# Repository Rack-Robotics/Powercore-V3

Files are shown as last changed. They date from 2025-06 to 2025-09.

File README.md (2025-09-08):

# Powercore V3

A high-efficiency power supply unit designed for Electrical Discharge Machining (EDM) applications.

## Repository Structure

- `circuit-boards/` - KiCAD PCB designs for all modules
- `schematics/` - Schematic PDFs for electronics
- `KiCAD-library/` - Custom component library and 3D models
- `LTSpice/` - Simulation files
- `powercoreV3-firmware/` - Arduino firmware for the RP2040 controller

## Table of Contents

- [PSU HIGHLIGHTS](#psu-highlights)
- [FEATURES](#features)
- [APPLICATIONS](#applications)
- [GENERAL DESCRIPTION](#general-description)
- [SPECIFICATIONS](#specifications)
- [Recommended Operating Conditions](#recommended-operating-conditions)
- [DEVICE INTERFACES](#device-interfaces)
  - [Power Input Connector](#power-input-connector)
  - [Power Output Connector](#power-output-connector)
  - [Digital Interface Connector](#digital-interface-connector)
  - [USB-Micro Serial Interface](#usb-micro-serial-interface)
- [THEORY OF OPERATION](#theory-of-operation)
- [OPERATION MODES](#operation-modes)
  - [Startup Behavior](#startup-behavior)
  - [Idle Mode](#idle-mode)
  - [Iso-Frequency Mode](#iso-frequency-mode)
  - [Edge-Detection Mode](#edge-detection-mode)
- [APPLICATION EXAMPLE: MINIMUM IMPLEMENTATION](#application-example-minimum-implementation)
- [EMC & EMI](#emc--emi)
- [Images of PCBA](#images-of-pcba)
- [Typical PSU Waveforms](#typical-psu-waveforms)
- [LICENSE](#license)
- [⚠️ HIGH VOLTAGE SAFETY WARNING ⚠️](#️-high-voltage-safety-warning-️)

## PSU HIGHLIGHTS

1. Optimized for wire EDM applications
2. Maximum input power: 300W with high efficiency topology
3. Adjustable output parameters:
   - Machining Duty Cycle: 1% to 10%
   - Spark Initiation Voltage: 64V to 100V
   - Machining Frequency: 5kHz to 10kHz
4. USB serial interface for configuration and telemetry
5. PWM feedback output for external feedrate control
6. Edge detection capability for workpiece probing

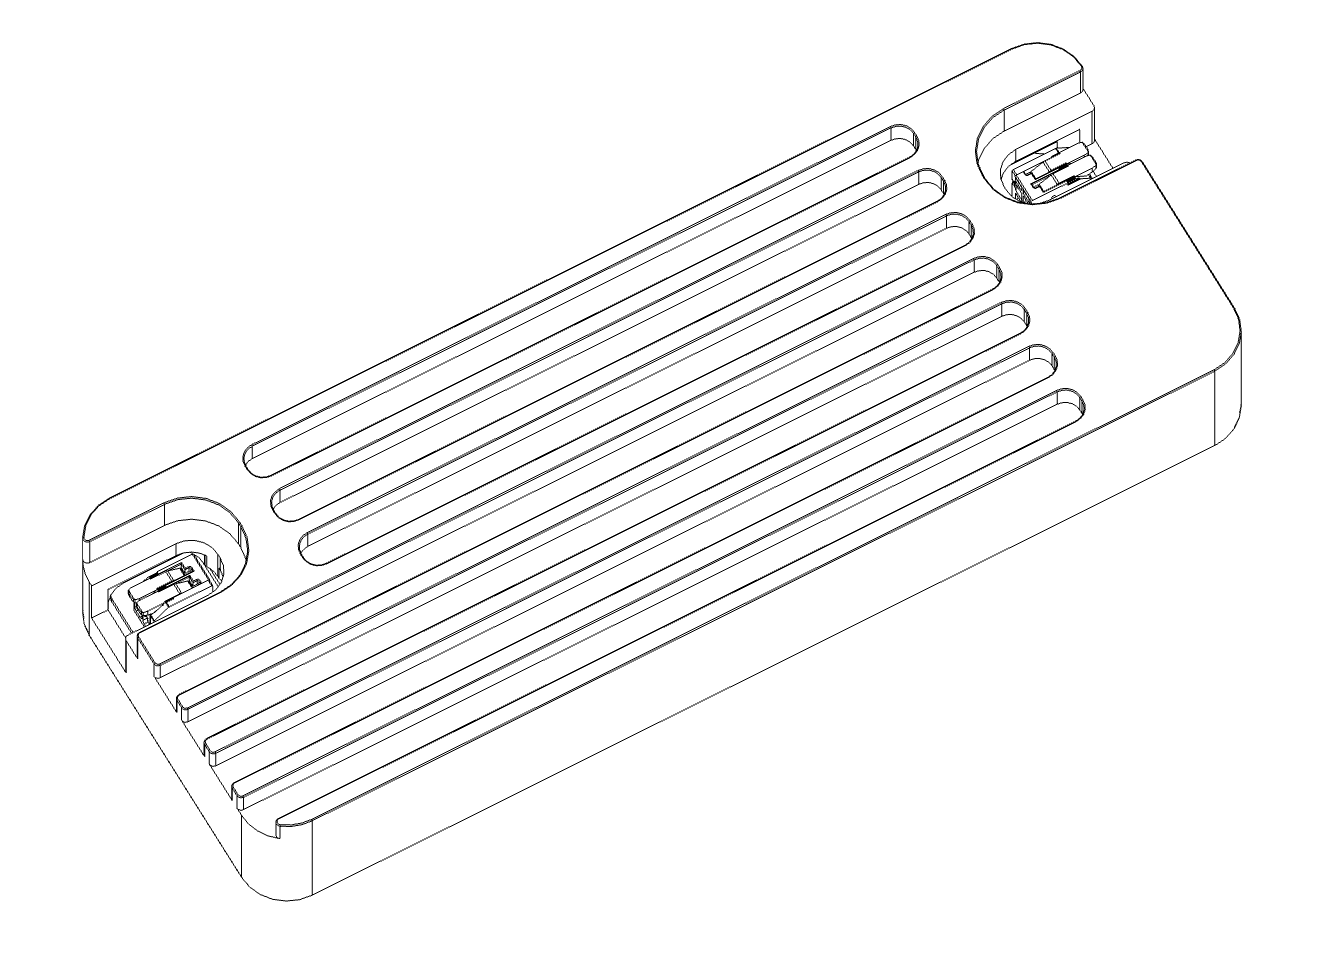
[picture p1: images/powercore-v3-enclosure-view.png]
Powercore V3 Enclosure View


## FEATURES

- **Dual-Converter Topology** with resonant converter and boost converter for high-efficiency EDM machining
- Input power optimized for desktop/micro-scale wire EDM (300W maximum, 48V input)
- Output parameters configurable via USB-micro serial interface
- Integrated protection features: pulse-skipping, overcurrent protection, and inrush protection
- Open-source electronics, firmware, and CAD files

## APPLICATIONS

- Wire EDM
- Plunge EDM
- Desktop-scale EDM machines
- Portable and battery-powered EDM machines
- Scientific research and development

## GENERAL DESCRIPTION

The Powercore V3 provides precision control of machining parameters including duty cycle, spark initiation voltage, and machining frequency. The system is optimized for desktop-scale wire EDM applications. The open-source design enables customization for research, development, and specialized EDM implementations.

## SPECIFICATIONS

| SPECIFICATION | Min | Max Value | UNIT |
| --- | --- | --- | --- |
| Average Input Power | 10 | 300 | W |
| Input Voltage | 47.8 | 48.2 | V |
| Input Current | 0.625 | 6.25 | A |
| Machining Duty Cycle | 1 | 10 | % |
| Spark Initiation Voltage | 64 | 100 | V |
| Machining Frequency | 5,000 | 10,000 | Hz |
| Machining Current (1) | 40 | 70 | A |
| PWM Feedback Duty Cycle | 0 | 100 | % |
| PWM Feedback Voltage | 0 | 3.3 | V |
| PWM Feedback Frequency  | — | 1,000 | Hz |
| PWM Feedback Output Impedance | 1,010 | 9,990 | Ω |
| Enable Input Voltage | 3.0 | 3.5 | V |
| Enable Input Impedance | 1,010 | 9,990 | Ω |

(1) Machining current depends on output cable impedance and discharge characteristics. Not regulated by constant-current control. Lower-impedance output cables provide higher machining current.

## Recommended Operating Conditions

| Parameter | Value |
| --- | --- |
| Ambient Temperature | 0°C to 30°C |
| Ingress Protection Rating | IP20 (Indoor use) |
| Relative Humidity | 20% to 80% (non-condensing) |
| Input Cable Gauge | 16 AWG minimum |
| Output Cable Gauge | 16 AWG stranded, 300V rated |
| Output Cable Length | <1 meter, twisted pair |
| Cooling | Forced air cooling recommended |

## DEVICE INTERFACES

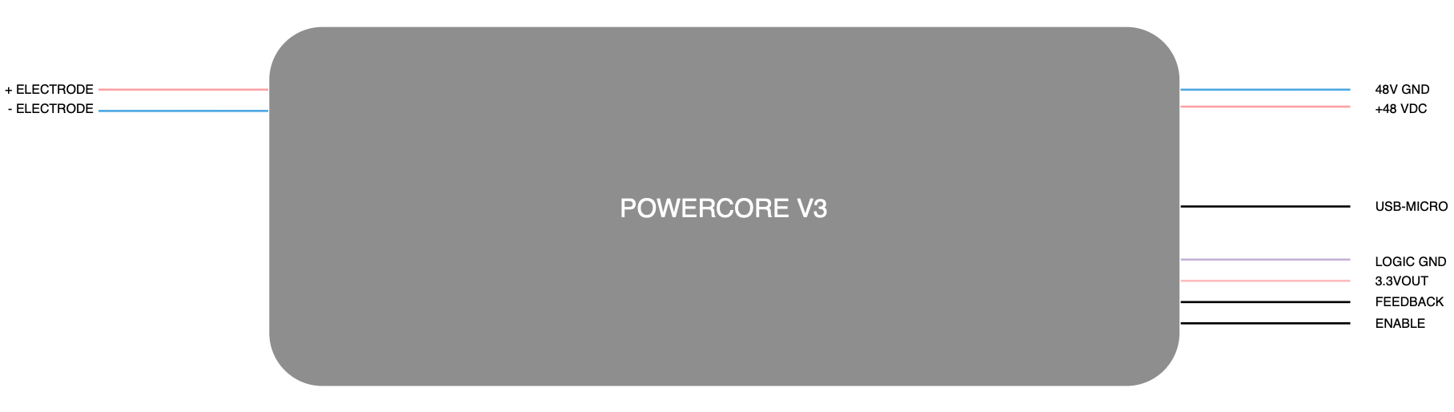
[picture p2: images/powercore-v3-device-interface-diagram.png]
Powercore V3 Device Interface Diagram


### POWER INPUT CONNECTOR

Input power connects via 2-position lever-action Wago connector accepting 16 AWG conductors. 48VDC input must be connected before applying 5V via USB-micro. If USB power is applied before 48VDC input, the microcontroller enters fault mode.

### POWER OUTPUT CONNECTOR 

Output connects via 2-position lever-action Wago connector accepting 16 AWG stranded conductors. Output cable must be twisted pair, <1 meter length, and either shielded/grounded or contained within a shielded/grounded enclosure.

### DIGITAL INTERFACE CONNECTOR 

4-position JST-XH header provides communication with external controllers. Exposes 3.3V and GND from RP2040 microcontroller with current-limiting resistors.

- **Enable Input**: Output is enabled when this input is connected to 3.3V or external 3.3V supply with common ground. 10kΩ pull-down resistor to GND.
- **Feedback Output**: Reports EDM power consumption via active-low PWM signal. 100% duty cycle indicates no power consumption from machining; 0% indicates short circuit. Maintain 10-90% duty cycle during machining by adjusting feedrate. 10kΩ pull-down resistor to GND. External low-pass filter can convert to analog feedback.

### USB-MICRO SERIAL INTERFACE

Exposes USB-micro connector of RP2040 Pico module for parameter configuration and telemetry. Default baud rate: 115,200.

**Warning**: Device requires both 48VDC input power AND 5V USB power. 48VDC must be connected first, or device enters fault mode.

| SERIAL COMMAND | DESCRIPTION |
| --- | --- |
| SEND_TELEMETRY | Request device status and parameters |
| SET_ALL_PARAMETERS | Configure machining parameters: discharges, duty cycle, frequency, initiation voltage<br>Format: 'SET_ALL_PARAMETERS [discharges] [duty_cycle] [frequency] [voltage]'<br>Example: 'SET_ALL_PARAMETERS 0 0.10 5000 100' |
| EDM_ISOFREQUENCY_MODE | Enter EDM iso-frequency mode |
| EDGE_DETECTION_MODE | Enter edge detection mode |
| RESET_DEVICE | Reset device |

Invalid commands return list of valid commands.

## THEORY OF OPERATION

The Powercore V3 generates controlled electrical discharges for EDM machining. The system cycles through spark initiation, current delivery, and discharge termination at high frequency (5-20kHz).

**Spark Initiation Voltage**: Determines spark formation conditions. Higher voltages create longer, more intense discharges suitable for harder materials.

**Machining Duty Cycle**: Controls discharge duration. Longer duty cycles increase material removal rate but may increase surface roughness.

**Machining Frequency**: Sets discharge repetition rate. Lower frequencies can increase material removal rate but may reduce surface finish quality.

**Machining Current**: Ranges from 40A to 70A, determined by fixed 48VDC output during current phase and combined impedance of output cables and discharge gap. Current is not user-adjustable.

## OPERATION MODES

### STARTUP BEHAVIOR 

On power-up, output is disabled (high-impedance state). Power management module initializes and pi-filter capacitors charge to 48V with inrush protection. Brief audible noise (~1 second) is normal during startup. Output current sensor calibrates and serial communication establishes.

**BOOST CONVERTER SELF-TEST**: System tests boost converter module and I2C digital potentiometer. If I2C communication fails, device reports 'ERROR: DPOT is not at expected position'. 

During startup, digital potentiometer cycles through settings 0-110, generating boost converter output voltage lookup table (50V-160V). If voltage range is insufficient, device enters fault mode and reports 'ERROR: DPOT voltage range is less than expected'.

Normal startup sequence via serial:
```
Setting DPOT to minimum position...
Waiting for voltage to stabilize...
Reading voltages for DPOT lookup table...
Boost Converter Digital Potentiometer Voltage Table:
0: 51
1: 52
...
109: 161
110: 166
```

Successful startup indicated by solid green LED and "Setup complete" message. Device enters IDLE mode.

### IDLE MODE

Output remains in high-impedance state until enable input is asserted (3.3V). No discharges occur in idle mode.

### ISO-FREQUENCY MODE

Fixed-frequency discharge mode. Default mode or activated via 'EDM_ISOFREQUENCY_MODE' command. Enable input must be asserted (3.3V) to begin operation.

**ISO-FREQUENCY MODE PARAMETERS**

| PARAMETER | Min | Default | Max | Unit |
| --- | --- | --- | --- | --- |
| Machining Duty Cycle | 1 | 10 | 10 | % |
| Machining Frequency | 5,000 | 1,000 | 10,000 | Hz |
| Spark Initiation Voltage | 64 | 80 | 100 | V |

### EDGE-DETECTION MODE

Probe mode for detecting electrode-workpiece contact via PWM feedback. Intended for setup and calibration only, not for machining. Activated via 'EDGE_DETECTION_MODE' command with enable input asserted.

## APPLICATION EXAMPLE: MINIMUM IMPLEMENTATION

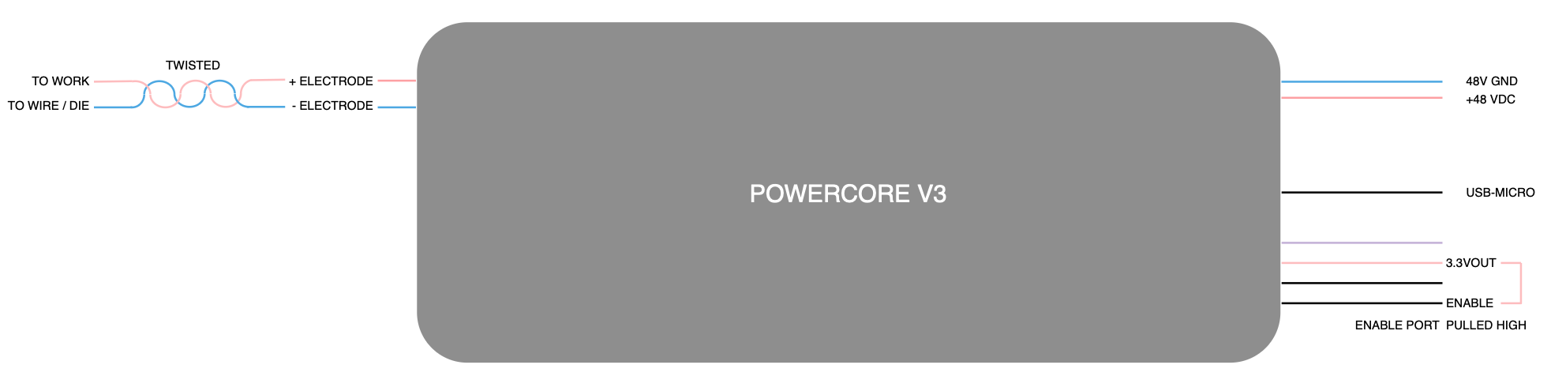
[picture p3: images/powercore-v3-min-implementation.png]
Powercore V3 Minimum Implementation


Minimum system configuration:

| Connection | Requirements |
| --- | --- |
| Power Input | 48V, 300W supply via 16 AWG stranded wire |
| USB-Micro | 5V supply or PC connection. **Note**: 48V must be connected first |
| Enable Input | Connect to 3.3V after power supplies are connected |
| Power Output | Positive (+) to workpiece, negative (-) to electrode (wire/tool) |

## EMC & EMI

The Powercore V3 power supply unit is housed in a precision-machined, billet-aluminum enclosure, fully grounded to minimize electromagnetic interference. When no output cables are connected, radiated emissions are negligible. However, when output cables are attached, radiated emissions vary based on cable characteristics, including length, twist, and wire gauge.

**Requirements**: Output cables must be shielded, grounded, and twisted. Poor cable design may increase emissions and interfere with sensitive equipment.

**Installation**: Complete machining setup should be enclosed, shielded, and grounded. EMC compliance is installer's responsibility.

## Images of PCBA

### PCBA View 1
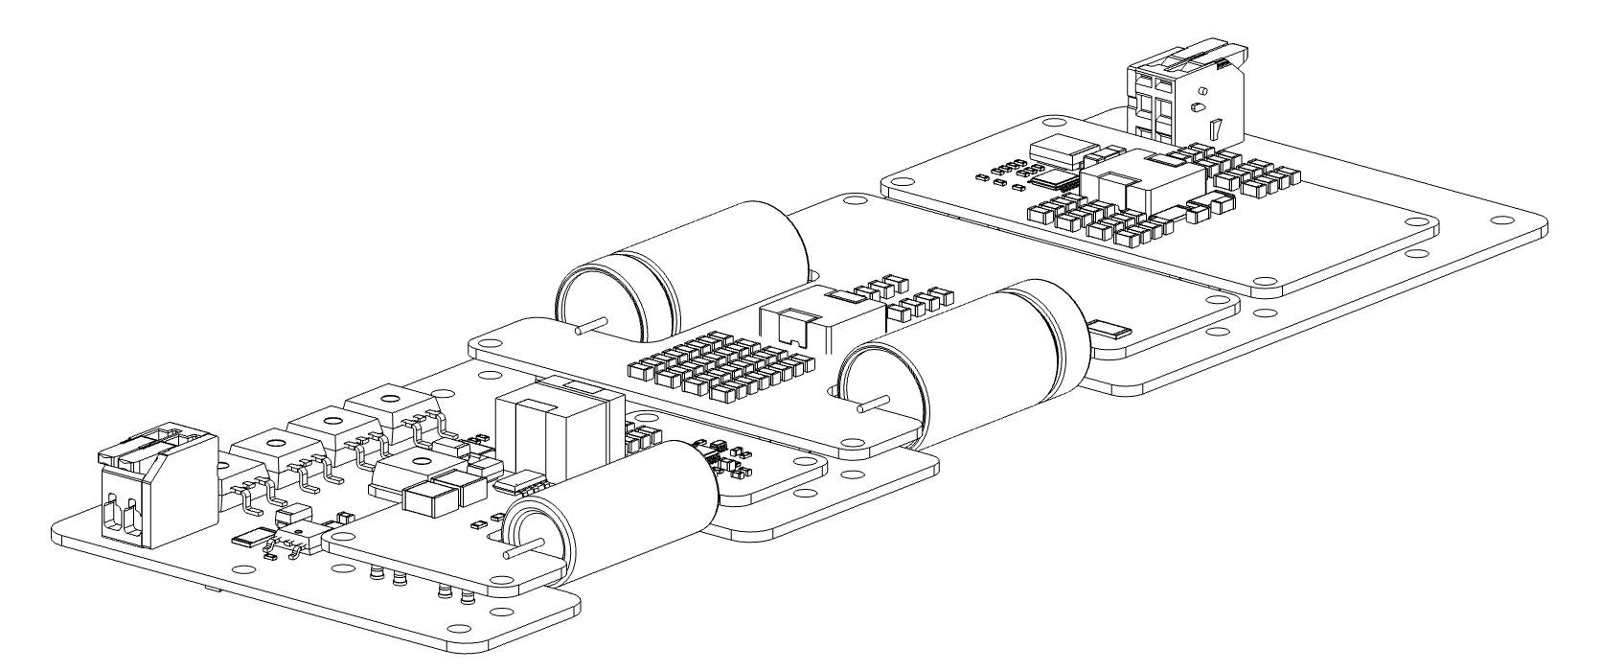
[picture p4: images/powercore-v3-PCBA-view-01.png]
Powercore V3 PCBA View 1


### PCBA View 2
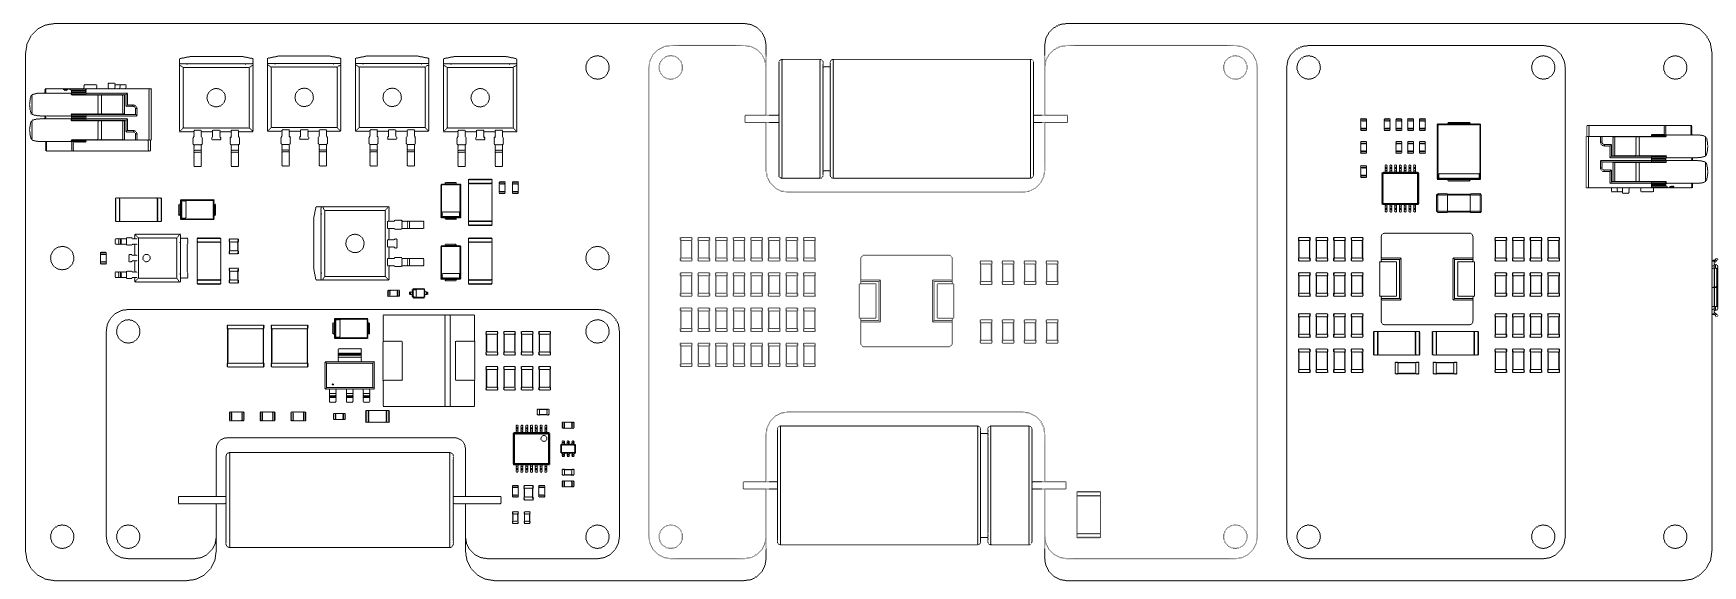
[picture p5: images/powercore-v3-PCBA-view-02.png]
Powercore V3 PCBA View 2


### PCBA View 3
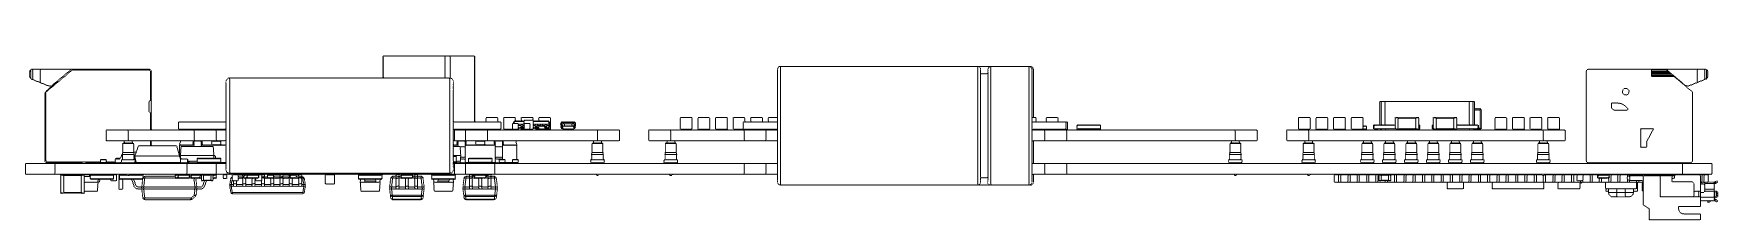
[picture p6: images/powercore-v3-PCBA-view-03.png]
Powercore V3 PCBA View 3


### PCBA View 4
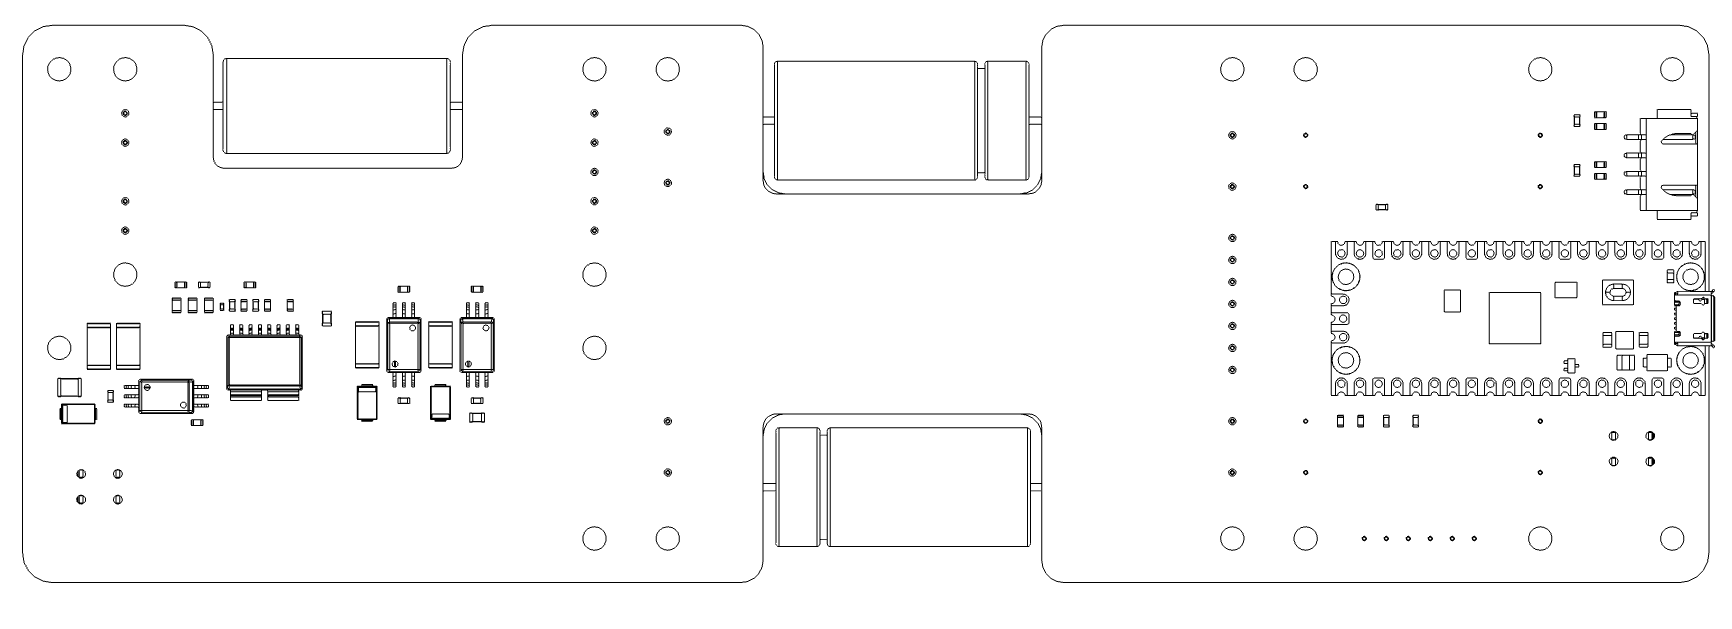
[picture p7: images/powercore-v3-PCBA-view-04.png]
Powercore V3 PCBA View 4


## Typical PSU Waveforms

### Output Stage Switch Control
Normal behavior of output stage switches during EDM iso-frequency mode. The enable (yellow trace) and high-current phase (red trace) switches are both active at the same time, permitting current flow from the positive electrode to the negative electrode. The high-voltage switch is active several microseconds before each switching event, for the purpose of charging the output capacitor to the spark initiation voltage (blue trace).

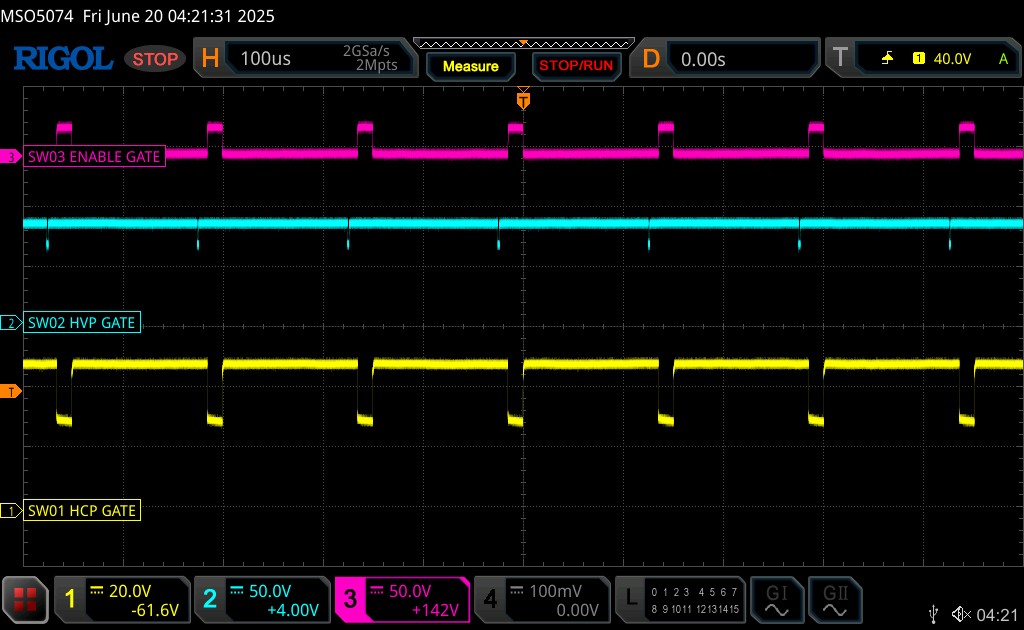
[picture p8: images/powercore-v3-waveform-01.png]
Powercore V3 Waveform 1


### Gap Voltage with Electrodes Separated
Normal behavior of output stages during EDM iso-frequency mode, with the electrodes separated by several millimeters under distilled water. The positive (+) electrode (red trace) shows the change in gap voltage when the output capacitor is charged and then slowly discharged through the water.

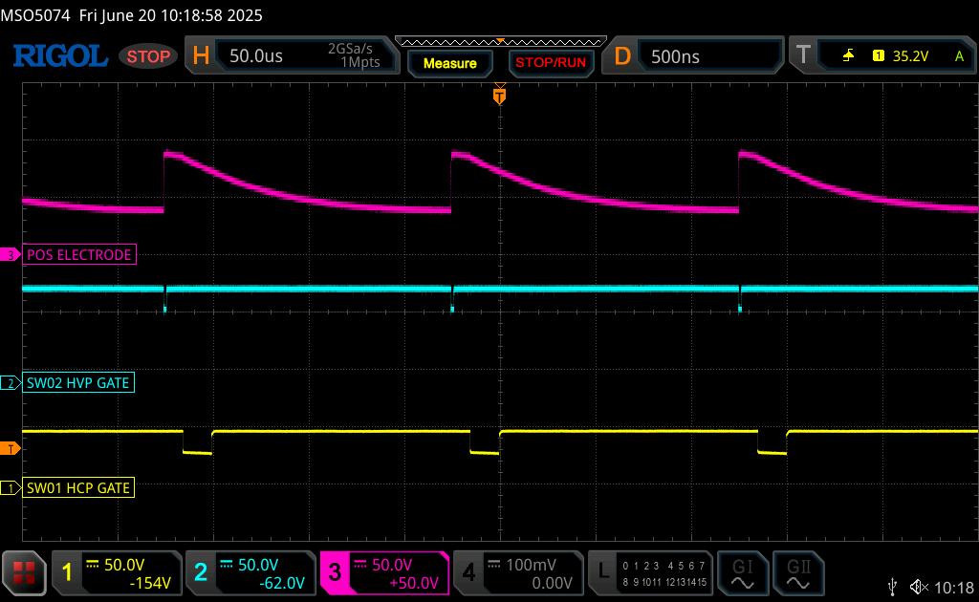
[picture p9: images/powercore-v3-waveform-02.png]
Powercore V3 Waveform 2


### EDM Discharge Behavior
Normal behavior of output stages during EDM iso-frequency mode, during electrical discharge machining. The positive (+) electrode voltage changes rapidly during an EDM discharge; transitioning from the spark initiation voltage (here 80V) to the gap machining voltage (~40V) in several hundred nanoseconds.

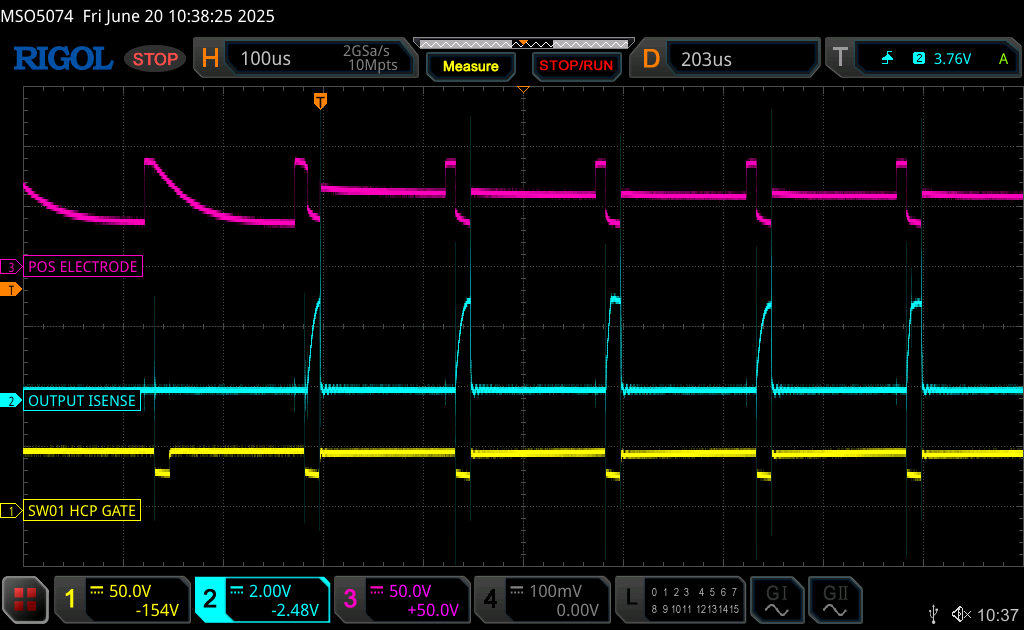
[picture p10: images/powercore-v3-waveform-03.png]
Powercore V3 Waveform 3


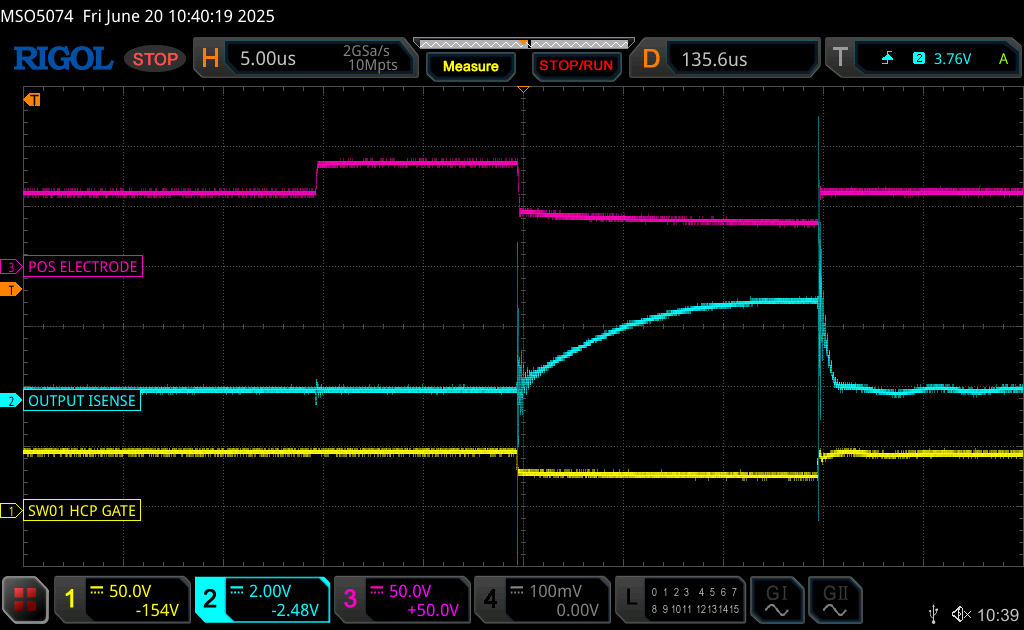
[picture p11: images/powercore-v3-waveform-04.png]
Powercore V3 Waveform 4


### Boost Converter Operation
Normal behavior of the boost converter module. The MOSFET gate (blue trace) presents with short pulses, which are used to maintain a stable output voltage. The output voltage will be set by the I2C digital potentiometer to between 64 and 150 V.

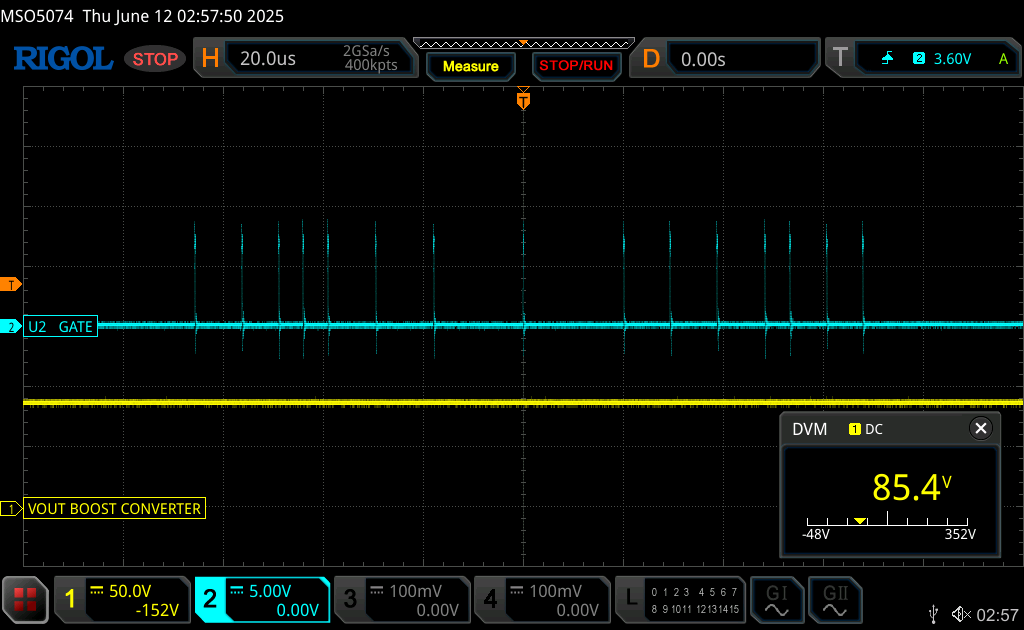
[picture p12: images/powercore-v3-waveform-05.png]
Powercore V3 Waveform 5


Startup behavior of device. Two seconds are required for inrush protection and serial communication initiation. Subsequently, the boost converter and output voltage sensor collaborate to create the lookup table for the I2C digital potentiometer. Once the lookup table is constructed, the boost converter is set to its default 80V setting.

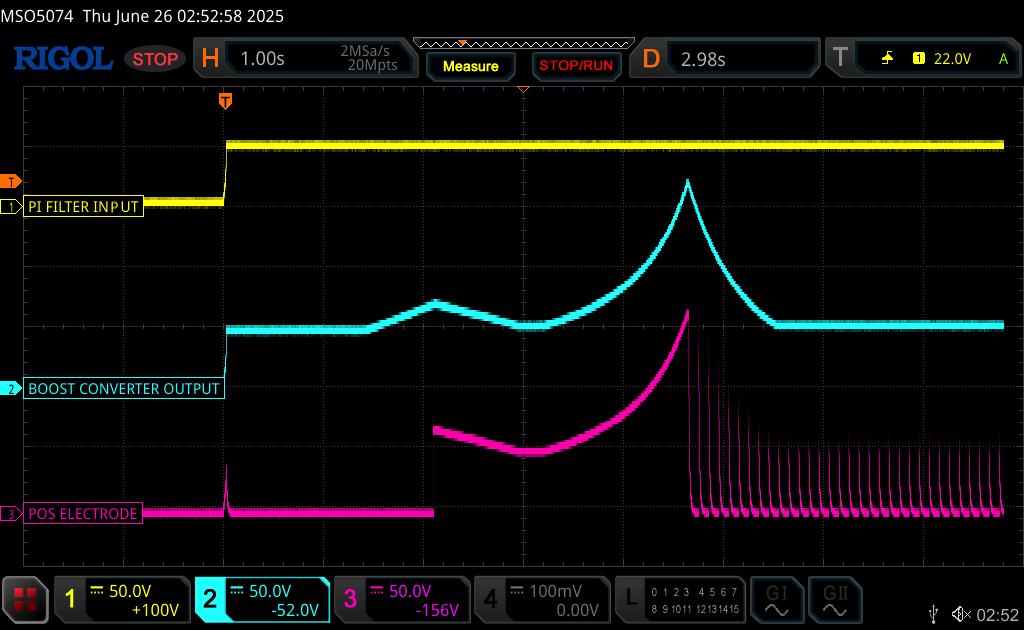
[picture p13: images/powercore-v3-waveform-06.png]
Powercore V3 Waveform 5


## LICENSE 
The Powercore V3 2025 by Rack Robotics, Inc. is licensed under the Creative Commons Attribution-NonCommercial-ShareAlike 4.0 International License (CC BY-NC-SA 4.0).

### You are free to:
- **Share** — copy and redistribute the material in any medium or format
- **Adapt** — remix, transform, and build upon the material

### Under the following terms:
- **Attribution** — You must give appropriate credit, provide a link to the license, and indicate if changes were made
- **NonCommercial** — You may not use the material for commercial purposes
- **ShareAlike** — If you remix, transform, or build upon the material, you must distribute your contributions under the same license as the original
- **No additional restrictions** — You may not apply legal terms or technological measures that legally restrict others from doing anything the license permits

### Notices:
You do not have to comply with the license for elements of the material in the public domain or where your use is permitted by an applicable exception or limitation.

No warranties are given. The license may not give you all of the permissions necessary for your intended use. For example, other rights such as publicity, privacy, or moral rights may limit how you use the material.

For the full license text, see: https://creativecommons.org/licenses/by-nc-sa/4.0/

This includes all hardware designs, firmware, documentation, and associated files in this repository. Commercial use requires explicit written permission from the project maintainers. 

### Trademark
The name 'Powercore' and 'Rack Robotics' are property of Rack Robotics, Inc. and are only to be used by Rack Robotics, Inc. Any derivative works must remove both marks unless written permission to use either or both marks is provided by Rack Robotics, Inc.

## ⚠️ HIGH VOLTAGE SAFETY WARNING ⚠️

**DANGER - HIGH VOLTAGE PRESENT**
This device generates and outputs high-voltage DC, which could be hazardous. Before operating, building, or servicing this equipment, read and understand all safety warnings.

ELECTRICAL HAZARDS
- **DANGEROUS VOLTAGES PRESENT**: Output voltages up to 150V DC can cause electrical shock or burns
- **STORED ENERGY**: Internal capacitors retain dangerous voltages even when power is disconnected
- **DISCHARGES**: High-energy discharges can cause burns, eye damage, and ignite flammable materials

LEGAL DISCLAIMER
- Users assume all responsibility for safe operation and compliance with local electrical codes
- This equipment is intended for use by qualified professionals only
- Improper use may result in serious injury, death, or property damage
- The manufacturer disclaims all liability for injuries or damages resulting from improper use
**IF YOU ARE NOT QUALIFIED TO WORK WITH HIGH-VOLTAGE EQUIPMENT, DO NOT PROCEED**

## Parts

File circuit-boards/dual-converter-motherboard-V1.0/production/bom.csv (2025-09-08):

Designator | Footprint | Quantity | Value | LCSC Part #
C1, C10, C13, C6, C8, C9 | 0603 | 6 | 220 nF | C726565
C11 | 1210 | 1 | 0.1 uF | C141218
C14, C15, C16, C2 | 0603 | 4 | 10000 pF | C115056
C3 | 0805 | 1 | 10 nF | C342860
C7 | 0805 | 1 | 0.47 uF | C596323
D1, D2, D8 | D_SMA | 3 | US1M-13-F | C99333
D10, D6, D7 | D_SMA | 3 | D_Zener | C110525
D3, D4, D5 | STPSC20065GY-TR | 3 | STPSC20065GY-TR | C2965441
D9 | D_SOD-323 | 1 | D_Zener | C82043
J1, J2 | 2601-1102 | 2 | 2601-1102 | C7509568
J3 | S4B-XH-SM4-TB | 1 | S4B-XH-SM4-TB | C161861
L1 | 0402 | 1 | BBUP00100505330Y00 | C668299
POGO1, POGO10, POGO11, POGO12, POGO13, POGO14, POGO15, POGO16, POGO17, POGO18, POGO19, POGO2, POGO20, POGO21, POGO22, POGO23, POGO24, POGO25, POGO26, POGO27, POGO28, POGO29, POGO3, POGO30, POGO4, POGO5, POGO6, POGO7, POGO8, POGO9 | 0906-8-15-20-76-14-11-0 | 30 | 0906-8-15-20-76-14-11-0 | C5128298
Q1 | SUM110P08-11L-E3 | 1 | SUM110P08-11L-E3 | C2838509
Q2 | DMP45H4D9HK3-13 | 1 | DMP45H4D9HK3-13
Q3 | TO-263-2 | 1 | SIHB068N60EF-GE3 | C3009875
R1, R2 | 0603 | 2 | 1K | C22548
R10, R11, R8 | 0805 | 3 | 332K
R12, R14, R17, R20, R21, R25, R3, R4 | 0603 | 8 | 10K | C20161635
R13 | 2512 | 1 | 1R | C840599
R15, R19, R26 | 0603 | 3 | 100R | C20161635
R16, R27 | 2512 | 2 | 1K | C7038808
R18, R28, R29 | 0603 | 3 | 2.2K | C3032396
R22, R23 | 2512 | 2 | 12K | C2082818
R24, R7, R9 | 2512 | 3 | 10R
R5, R6 | 0603 | 2 | 255K | C295887
U1 | POWER_MANAGEMENT_MODULE_FOOTPRINT_V1.0 | 1 | POWER_MANAGEMENT_MODULE
U2 | HIGH-CURRENT_PHASE_MODULE_FOOTPRINT_V1.0 | 1 | HIGH-CURRENT_PHASE_MODULE_V1.0
U3 | HIGH-VOLTAGE_PHASE_MODULE_FOOTPRINT_V1.0 | 1 | HIGH-VOLTAGE_PHASE_MODULE
U4, U6, U7 | UCC23313BDWYR | 3 | UCC23313BDWYR | C2868027
U5 | TMCS1133C3AQDVGR | 1 | TMCS1133C1A | C32266987
U8 | SC0915 | 1 | SC0915 | C7203002

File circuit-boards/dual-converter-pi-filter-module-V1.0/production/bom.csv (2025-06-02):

Designator | Footprint | Quantity | Value | LCSC Part #
C1, C10, C11, C12, C13, C14, C15, C16, C17, C18, C19, C2, C20, C21, C22, C23, C24, C25, C26, C27, C28, C29, C3, C30, C31, C32, C33, C34, C35, C36, C37, C38, C39, C40, C41, C42, C5, C7, C8, C9 | 1206 | 40 | 10 uF | C96600
C4, C6 | PHA225 | 2 | 560 uF | C3274794
L1 | SRP1245A | 1 | 18uH | C5926042
R1 | 2512 | 1 | 4.7K | C878291

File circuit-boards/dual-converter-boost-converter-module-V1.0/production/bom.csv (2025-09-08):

Designator | Footprint | Quantity | Value | LCSC Part #
C1, C2, C3, C4, C6, C7, C8, C9 | 1206 | 8 | 10 uF | C96600
C10, C5 | 0603 | 2 | 1 uF | C106215
C11 | 0805 | 1 | 33 uF | C342635
C12 | 0603 | 1 | 39nF | C107091
C14 | 226TTA350M | 1 | 22UF | C6077372
C15, C16 | 2220 | 2 | 2.2 uF | C445674
D1 | D_SMA | 1 | US1M-13-F | C99333
L1 | SRR1210-681M | 1 | 680 uH | NULL
R1, R2, R3 | 0805 | 3 | 200K | C728645
R4, R5 | 0603 | 2 | 2.2K | C3032396
R6 | 0603 | 1 | 49.3K | C861433
R7 | 0603 | 1 | 15K | C855633
R8 | 0603 | 1 | 100K | C844916
R9 | 1206 | 1 | 90mR | C375525
U1 | TPL0401B-10DCKR | 1 | TPL0401B-10DCKR | C2666599
U2 | lm5156h | 1 | LM5156HPWPR | C2867852
U3 | STN3N40K3 | 1 | STN3N40K3 | C128261

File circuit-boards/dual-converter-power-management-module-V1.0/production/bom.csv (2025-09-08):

Designator | Footprint | Quantity | Value | LCSC Part #
C1 | 0603 | 1 | 1 uF | C106215
C10, C11, C12, C13, C14, C15, C16, C17, C18, C19, C2, C20, C21, C22, C23, C24, C25, C26, C27, C28, C29, C3, C30, C31, C32, C33, C34, C35, C4, C5, C6, C7, C8, C9 | 1206 | 34 | 10 uF | C96600
D1 | D_SMC | 1 | SMCJ60A-E3/57T | C1975272
L1 | SRP1245A | 1 | 18uH | C5926042
R1, R6, R7 | 0603 | 3 | 100K | C844916
R10, R13 | 2512 | 2 | 1R | C181756
R2, R3, R4, R5 | 0603 | 4 | 2.2K | C114662
R8 | 0603 | 1 | 249R | C861249
R9 | 0603 | 1 | 0R | C95177
U1 | TPS1HTC30-Q1 | 1 | TPS1HTC30AQPWPRQ1 | C22414694

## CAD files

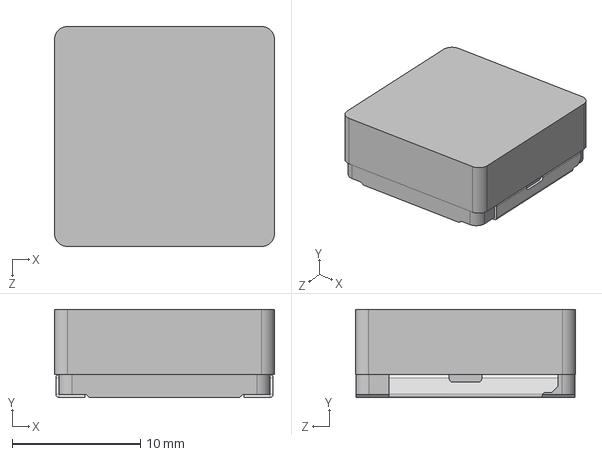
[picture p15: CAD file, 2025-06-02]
KiCAD-library/3D-models/IHLP6767GZER2R2M51.step
17.2 x 6.88 x 17.2 mm

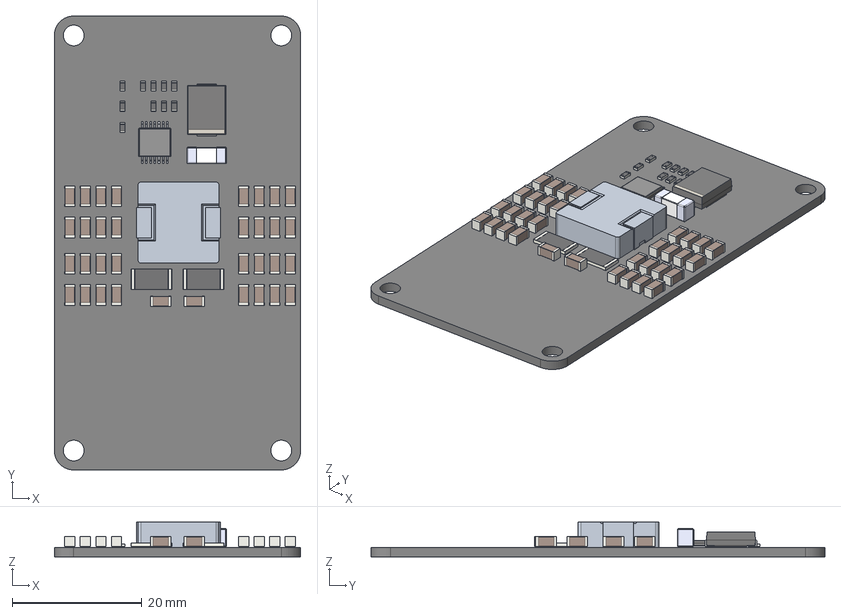
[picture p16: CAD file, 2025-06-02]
KiCAD-library/3D-models/power-management-module-V1.0.step
38.0 x 70.0 x 5.37 mm
C_1206_3216Metric x 34
BODY-SO
LEAD-SO x 14
THERMALPAD-SO
R_0603_1608Metric x 10
SRP1245A series
R_2512_6332Metric x 2
0679H9120-05
D_SMC
dual-converter-power-management-module-V1.0_PCB

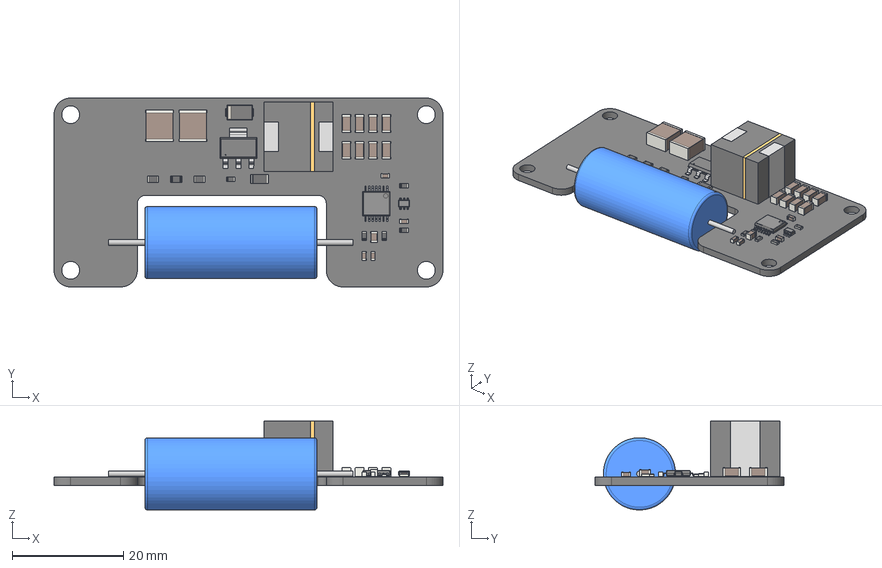
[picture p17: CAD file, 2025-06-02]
KiCAD-library/3D-models/boost-converter-module-V1.0.step
70.0 x 34.0 x 16.0 mm
C_0603_1608Metric x 4
R_0805_2012Metric x 3
R_1206_3216Metric
R_0603_1608Metric x 5
C_0805_2012Metric
SRR1210-681M
C_1206_3216Metric x 8
BODY-SOT
LEAD-SOT x 6
PIN1-ID
C_2220_5750Metric x 2
BODY-TSSOP
LEAD-TSSOP x 14
PIN1
DAP
STN3N40K3
226TTA350M
D_SMA
dual-converter-boost-converter-module-V1.0_PCB

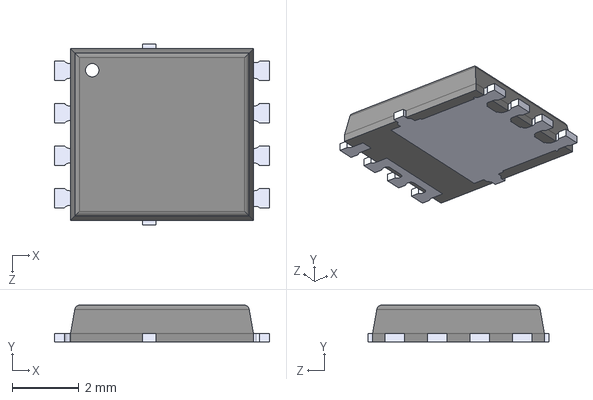
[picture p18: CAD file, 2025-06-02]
KiCAD-library/3D-models/IAUC70N08S5N074ATMA1.step
6.44 x 1.10 x 5.41 mm

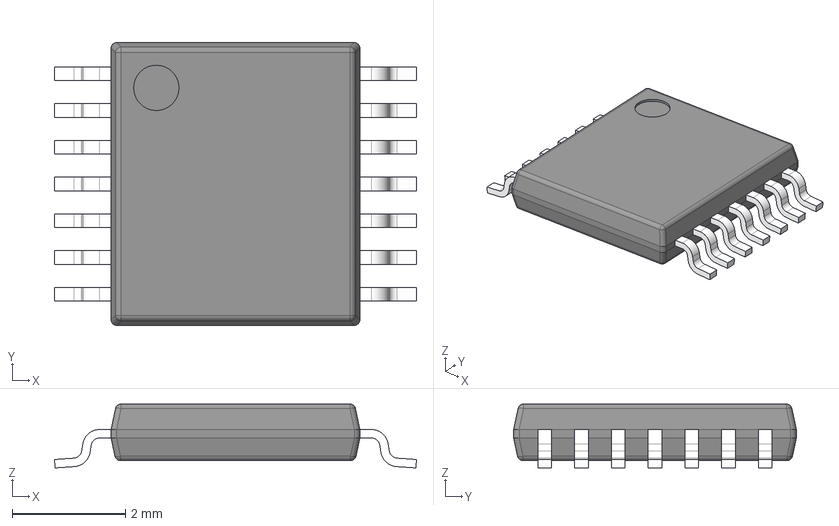
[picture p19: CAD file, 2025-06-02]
KiCAD-library/3D-models/lm5156h.stp
6.40 x 5.00 x 1.13 mm
BODY-TSSOP
LEAD-TSSOP x 14
PIN1
DAP

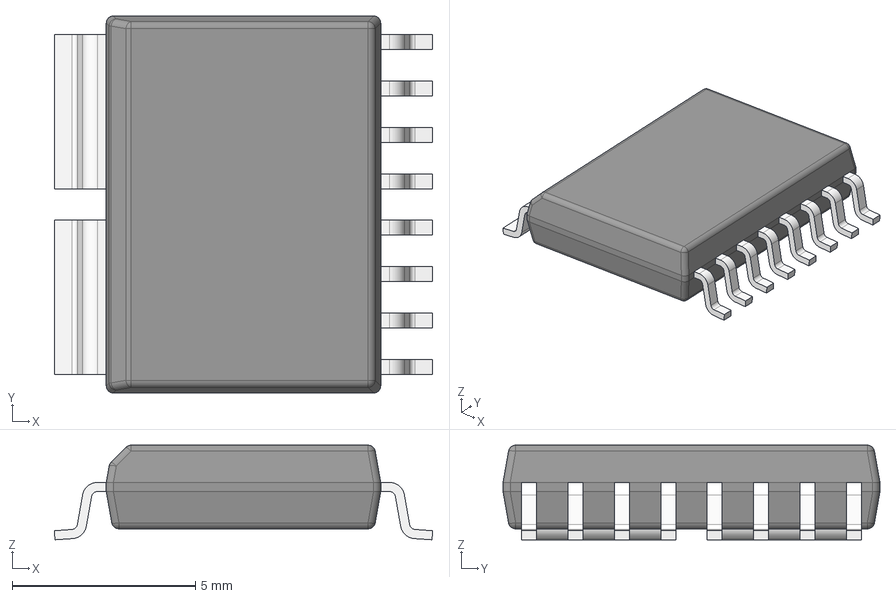
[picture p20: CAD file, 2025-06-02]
KiCAD-library/3D-models/TMCS1133C3AQDVGR.stp
10.3 x 10.3 x 2.59 mm
BODY-SOIC
LEAD x 8
LEAD_WIDE x 2

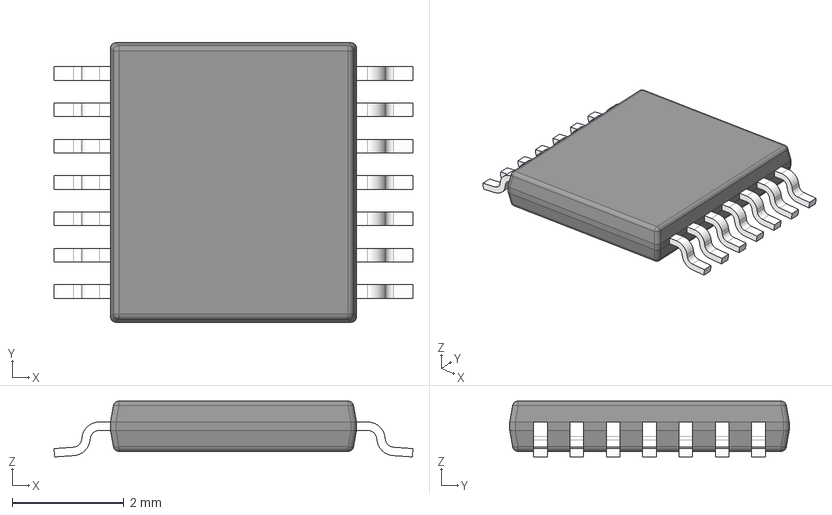
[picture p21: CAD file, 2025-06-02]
KiCAD-library/3D-models/TPS1HTC30-Q1.stp
6.42 x 5.00 x 1.00 mm
BODY-SO
LEAD-SO x 14
THERMALPAD-SO

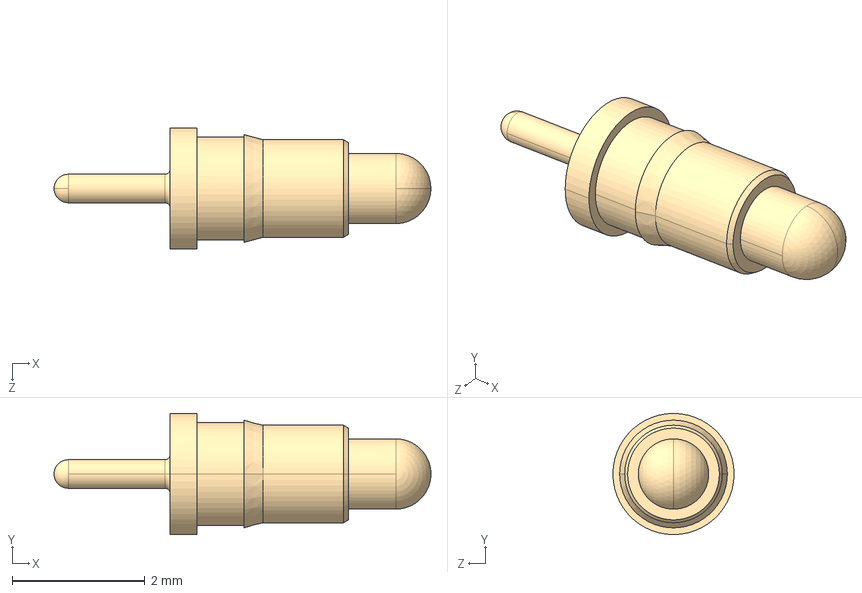
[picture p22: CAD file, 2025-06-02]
KiCAD-library/3D-models/0906-8-15-20-76-14-11-0.step
5.69 x 1.83 x 1.83 mm

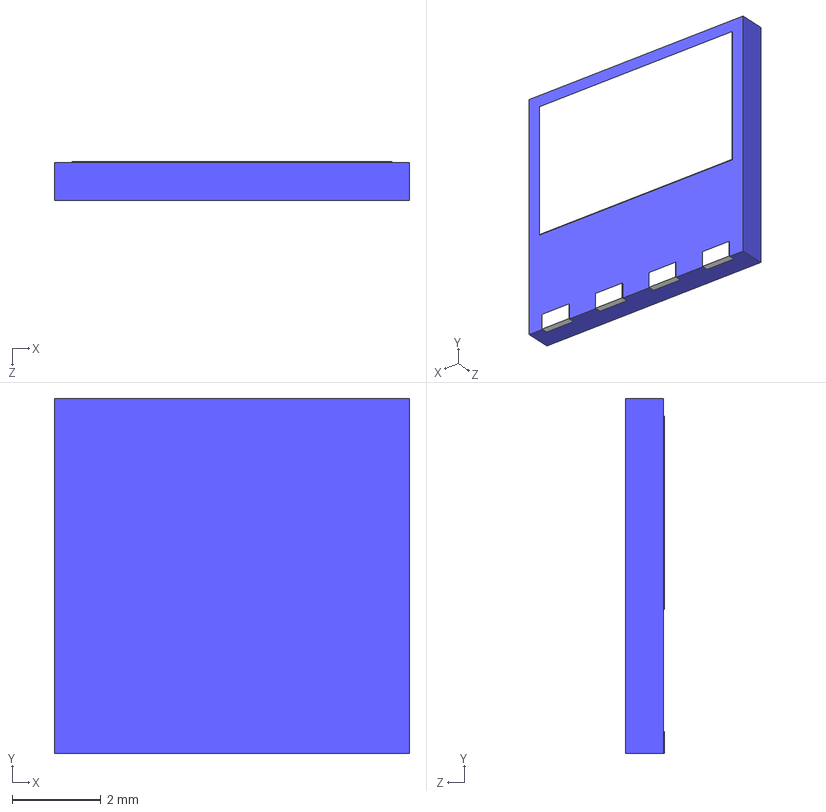
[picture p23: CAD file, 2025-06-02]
KiCAD-library/3D-models/TK31V60W5,LVQ.step
8.00 x 8.00 x 0.875 mm

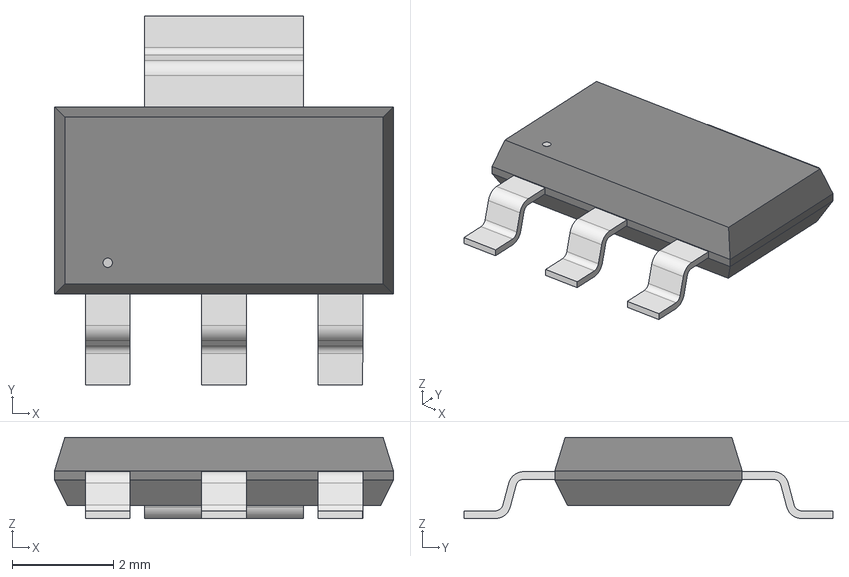
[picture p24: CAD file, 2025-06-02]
KiCAD-library/3D-models/STN3N40K3.step
6.71 x 7.29 x 1.60 mm

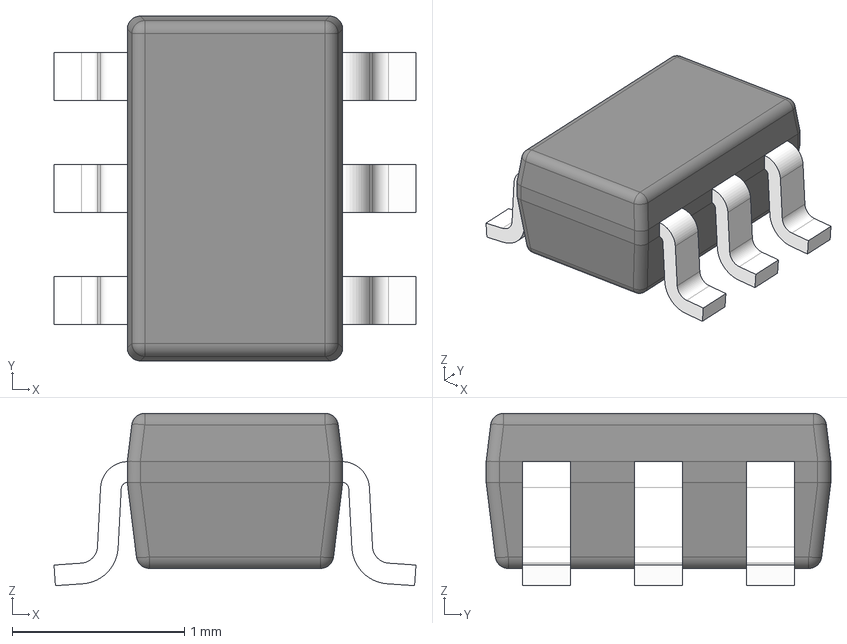
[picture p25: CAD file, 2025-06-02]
KiCAD-library/3D-models/TPL0401B-10DCKR.stp
2.10 x 2.00 x 1.00 mm
BODY-SOT
LEAD-SOT x 6
PIN1-ID

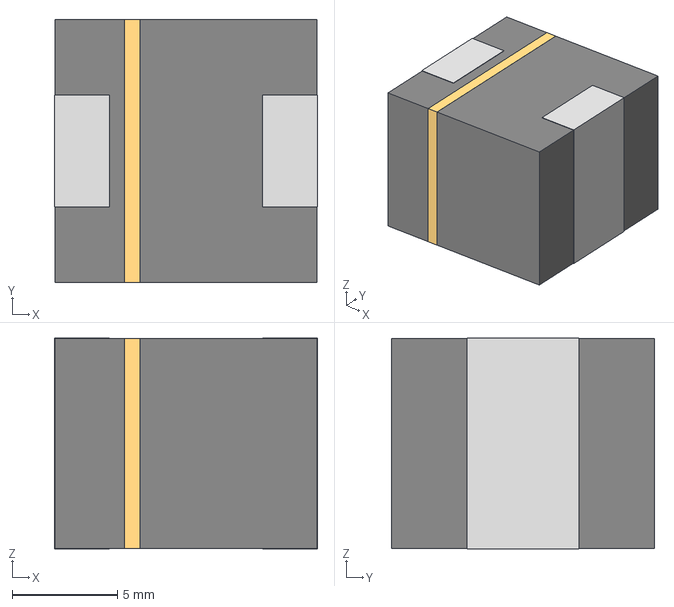
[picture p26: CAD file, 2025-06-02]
KiCAD-library/3D-models/SRR1210-681M.step
12.5 x 12.5 x 10.0 mm

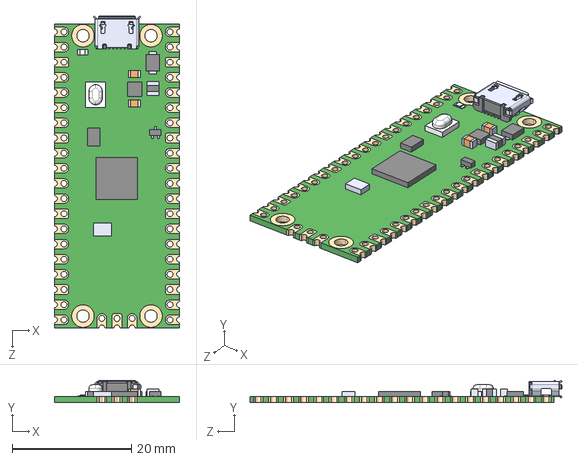
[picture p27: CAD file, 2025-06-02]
KiCAD-library/3D-models/SC0915.step
21.0 x 3.73 x 52.3 mm

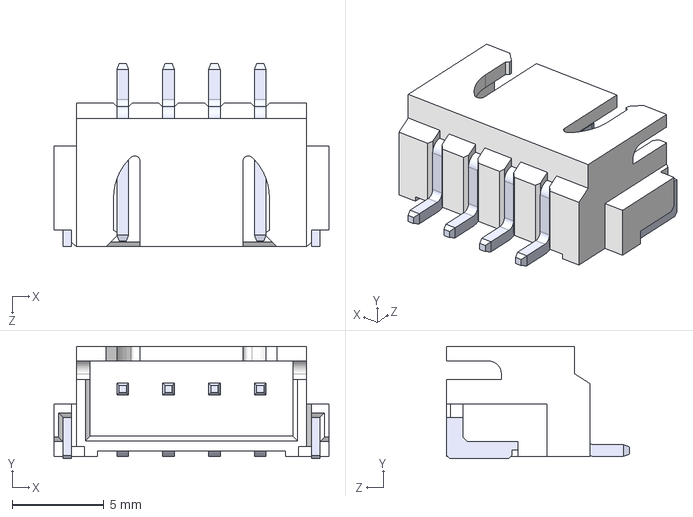
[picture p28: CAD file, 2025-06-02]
KiCAD-library/3D-models/S4B-XH-SM4-TB.STEP
15.0 x 6.12 x 10.0 mm
SxB-XH-SM4-TB_4
pin^SxB-XH-SM4-TB Ass x 4

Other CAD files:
KiCAD-library/3D-models/TMCS1108A3UQDRQ1.stp
KiCAD-library/3D-models/S3B-PH-SM4-TB.step
KiCAD-library/3D-models/226TTA350M.step
KiCAD-library/3D-models/BSZ070N08LS5ATMA1.step
KiCAD-library/3D-models/0679H9120-05.step
KiCAD-library/3D-models/2601-1102.stp
KiCAD-library/3D-models/2601-1108.stp
KiCAD-library/3D-models/430450409.step
KiCAD-library/3D-models/430450822.step
KiCAD-library/3D-models/BSZ146N10LS5ATMA1.step
KiCAD-library/3D-models/LM5149-Q1.stp
KiCAD-library/3D-models/PHA225.step
KiCAD-library/3D-models/SRP1245A series.stp
KiCAD-library/3D-models/UCC23313BDWYR.stp
KiCAD-library/3D-models/UHE1H272MHD.step
KiCAD-library/3D-models/pi-filter-module-V1.0.step

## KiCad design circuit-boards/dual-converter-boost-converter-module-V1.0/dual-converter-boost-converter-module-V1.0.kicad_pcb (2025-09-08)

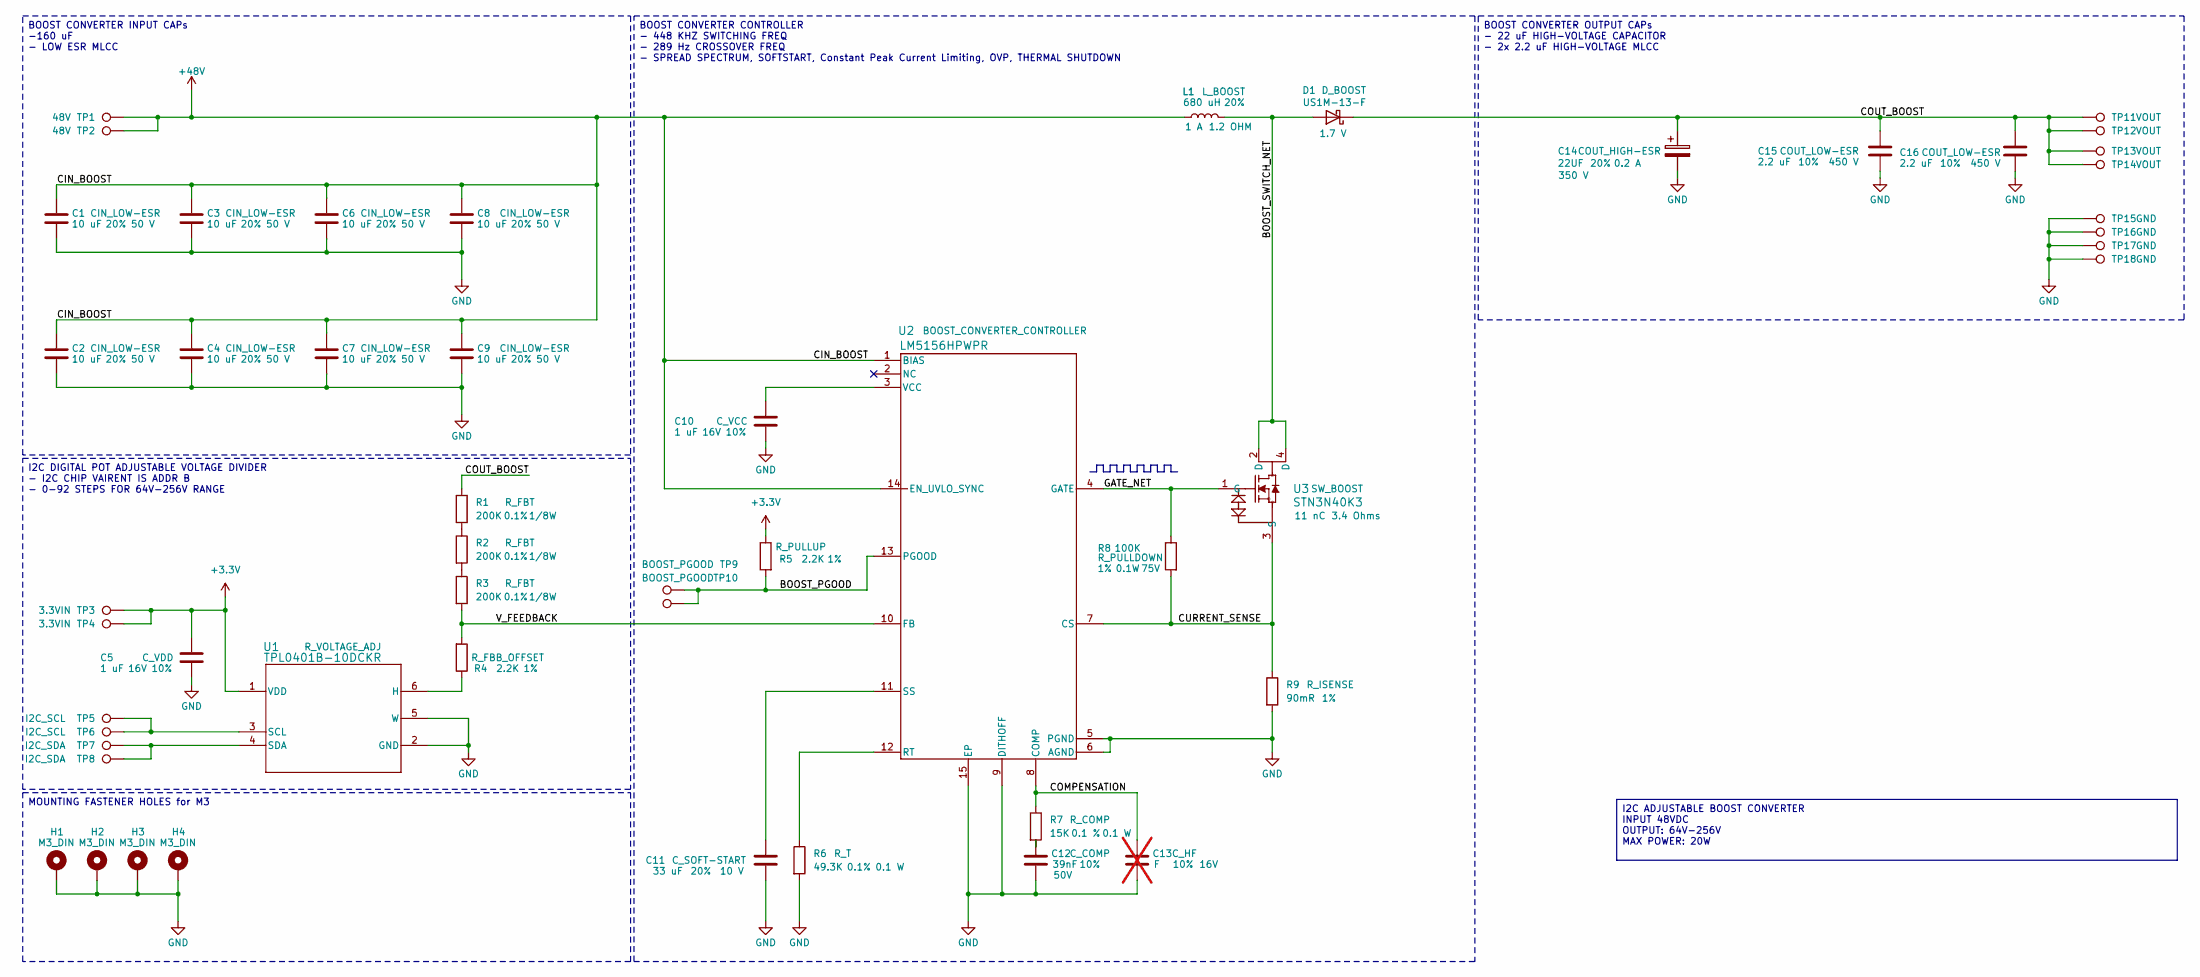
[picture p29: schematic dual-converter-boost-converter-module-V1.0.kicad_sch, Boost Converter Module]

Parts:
C1, C2, C3, C4, C6, C7, C8, C9: 10 uF; C_1206_3216Metric; Tolerance 20%; Max Voltage 50 V; Manufacturer# CL31A106MBHNNNE; LCSC Part # C96600
C5, C10: 1 uF; C_0603_1608Metric; Tolerance 10%; Max Voltage 16V; Manufacturer# CC0603KRX5R7BB105; LCSC Part # C106215
C11: 33 uF; C_0805_2012Metric; Tolerance 20%; Max Voltage 10 V; Manufacturer# C2012X5R1A336MTJ00E; LCSC Part # C342635
C12: 39nF; C_0603_1608Metric; Tolerance 10%; Max Voltage 50V; Manufacturer# CC0603KRX7R9BB393; LCSC Part # C107091
C13: F; C_0603_1608Metric; Tolerance 10%; Max Voltage 16V; Manufacturer# NULL; LCSC Part # NULL; not fitted
C14: 22UF; 226TTA350M; Tolerance 20%; Max Voltage 350 V; Manufacturer# 226TTA350M; LCSC Part # C6077372
C15, C16: 2.2 uF; C_2220_5750Metric; Tolerance 10%; Max Voltage 450 V; Manufacturer# TDK Corporation; LCSC Part # C445674
D1: US1M-13-F; D_SMA; Forward Voltage 1.7 V; Manufacturer# US1M-13-F; LCSC Part # C99333
H1, H2, H3, H4: M3_DIN; MountingHole_3.2mm_M3_DIN965_Pad_TopBottom; Manufacturer# NULL
L1: 680 uH; SRR1210-681M; Tolerance 20%; Manufacturer# SRR1210-681M; LCSC Part # NULL
R1, R2, R3: 200K; R_0805_2012Metric; Tolerance 0.1%; Manufacturer# RT0805BRD07200KL; LCSC Part # C728645
R4, R5: 2.2K; R_0603_1608Metric; Tolerance 1%; Manufacturer# 13-RC0603FR-132K2LCT-ND; LCSC Part # C3032396
R6: 49.3K; R_0603_1608Metric; Tolerance 0.1%; Manufacturer# AT0603BRD0749K3L; LCSC Part # C861433
R7: 15K; R_0603_1608Metric; Tolerance 0.1 %; Manufacturer# AT0603BRD0715KL; LCSC Part # C855633
R8: 100K; R_0603_1608Metric; Tolerance 1%; Max Voltage 75V; Manufacturer# CRCW0603100KFKEA; LCSC Part # C844916
R9: 90mR; R_1206_3216Metric; Tolerance 1%; Manufacturer# RL1206FR-070R09L; LCSC Part # C375525
TP1, TP2: 48V; TestPoint_TestPoint_Pad_2.0x2.0mm_No_Silkscreen; Manufacturer# NULL
TP3, TP4: 3.3VIN; TestPoint_TestPoint_Pad_2.0x2.0mm_No_Silkscreen; Manufacturer# NULL
TP5, TP6: I2C_SCL; TestPoint_TestPoint_Pad_2.0x2.0mm_No_Silkscreen; Manufacturer# NULL
TP7, TP8: I2C_SDA; TestPoint_TestPoint_Pad_2.0x2.0mm_No_Silkscreen; Manufacturer# NULL
TP9, TP10: BOOST_PGOOD; TestPoint_TestPoint_Pad_2.0x2.0mm_No_Silkscreen; Manufacturer# NULL
TP11, TP12, TP13, TP14: VOUT; TestPoint_TestPoint_Pad_2.0x2.0mm_No_Silkscreen; Manufacturer# NULL
TP15, TP16, TP17, TP18: GND; TestPoint_TestPoint_Pad_2.0x2.0mm_No_Silkscreen; Manufacturer# NULL
U1: TPL0401B-10DCKR; Manufacturer# TPL0401B-10DCKR; LCSC Part # C2666599
U2: LM5156HPWPR; lm5156h; Manufacturer# LM5156HPWPR; LCSC Part # C2867852
U3: STN3N40K3; Manufacturer# STN3N40K3; LCSC Part # C128261

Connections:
+3.3V: C5.1, R5.1, TP3.1, TP4.1, U1.1 (VDD)
+48V: C1.1, C2.1, C3.1, C4.1, C6.1, C7.1, C8.1, C9.1, L1.1, TP1.1, TP2.1, U2.1 (BIAS), U2.14 (EN_UVLO_SYNC)
/BOOST_PGOOD: R5.2, TP9.1, TP10.1, U2.13 (PGOOD)
/BOOST_SWITCH_NET: D1.2 (A), L1.2, U3.2 (D), U3.4 (D)
/COMPENSATION: C13.1, R7.1, U2.8 (COMP)
/COUT_BOOST: C14.1, C15.1, C16.1, D1.1 (K), R1.1, TP11.1, TP12.1, TP13.1, TP14.1
/CURRENT_SENSE: R8.2, R9.1, U2.7 (CS), U3.3 (S)
/GATE_NET: R8.1, U2.4 (GATE), U3.1 (G)
/V_FEEDBACK: R3.2, R4.2, U2.10 (FB)
GND: C1.2, C2.2, C3.2, C4.2, C5.2, C6.2, C7.2, C8.2, C9.2, C10.2, C11.2, C12.2, C13.2, C14.2, C15.2, C16.2, H1.1, H2.1, H3.1, H4.1, R6.2, R9.2, TP15.1, TP16.1, TP17.1, TP18.1, U1.2 (GND), U1.5 (W), U2.5 (PGND), U2.6 (AGND), U2.9 (DITHOFF), U2.15 (EP)
unnamed: C12.1, R7.2
unnamed: R1.2, R2.1
unnamed: R2.2, R3.1
unnamed: R4.1, U1.6 (H)
unnamed: TP5.1, TP6.1, U1.3 (SCL)
unnamed: TP7.1, TP8.1, U1.4 (SDA)
unnamed: R6.1, U2.12 (RT)
unnamed: C11.1, U2.11 (SS)
unnamed: C10.1, U2.3 (VCC)

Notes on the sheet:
BOOST CONVERTER CONTROLLER - 448 KHZ SWITCHING FREQ - 289 Hz CROSSOVER FREQ - SPREAD SPECTRUM, SOFTSTART, Constant Peak Current Limiting, OVP, THERMAL SHUTDOWN
BOOST CONVERTER INPUT CAPs -160 uF - LOW ESR MLCC
I2C DIGITAL POT ADJUSTABLE VOLTAGE DIVIDER - I2C CHIP VAIRENT IS ADDR B - 0-92 STEPS FOR 64V-256V RANGE
MOUNTING FASTENER HOLES for M3
BOOST CONVERTER OUTPUT CAPs - 22 uF HIGH-VOLTAGE CAPACITOR - 2x 2.2 uF HIGH-VOLTAGE MLCC
I2C ADJUSTABLE BOOST CONVERTER INPUT 48VDC OUTPUT: 64V-256V MAX POWER: 20W

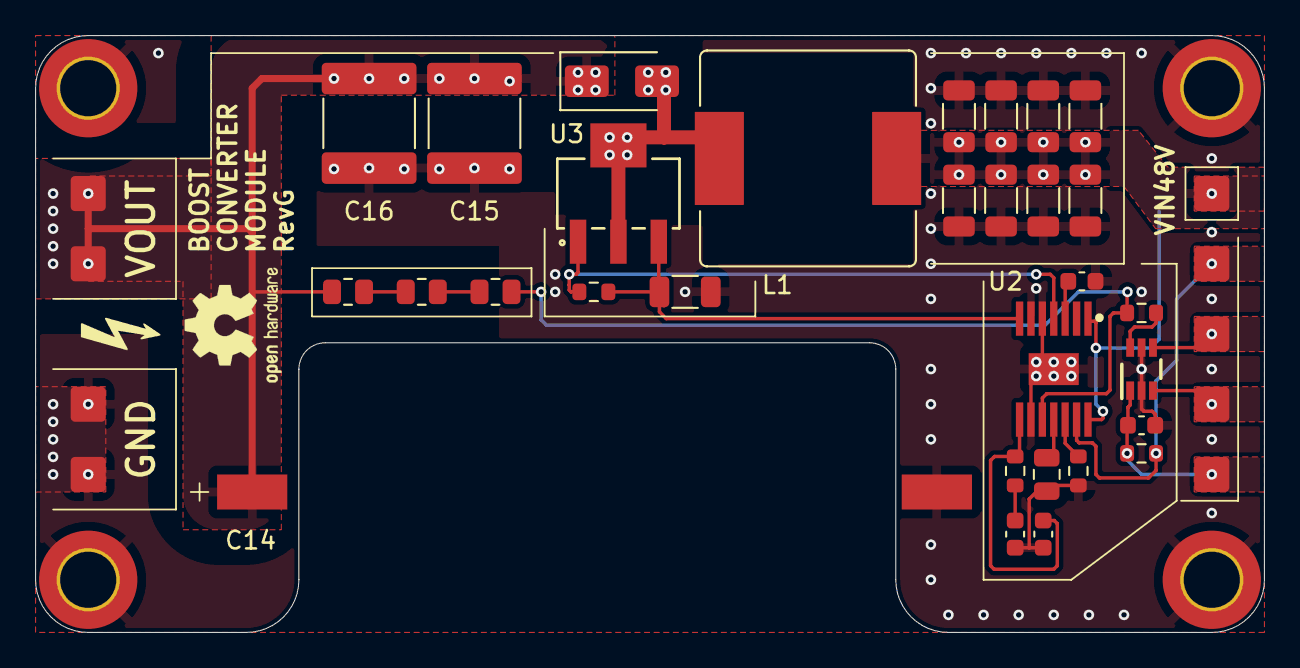
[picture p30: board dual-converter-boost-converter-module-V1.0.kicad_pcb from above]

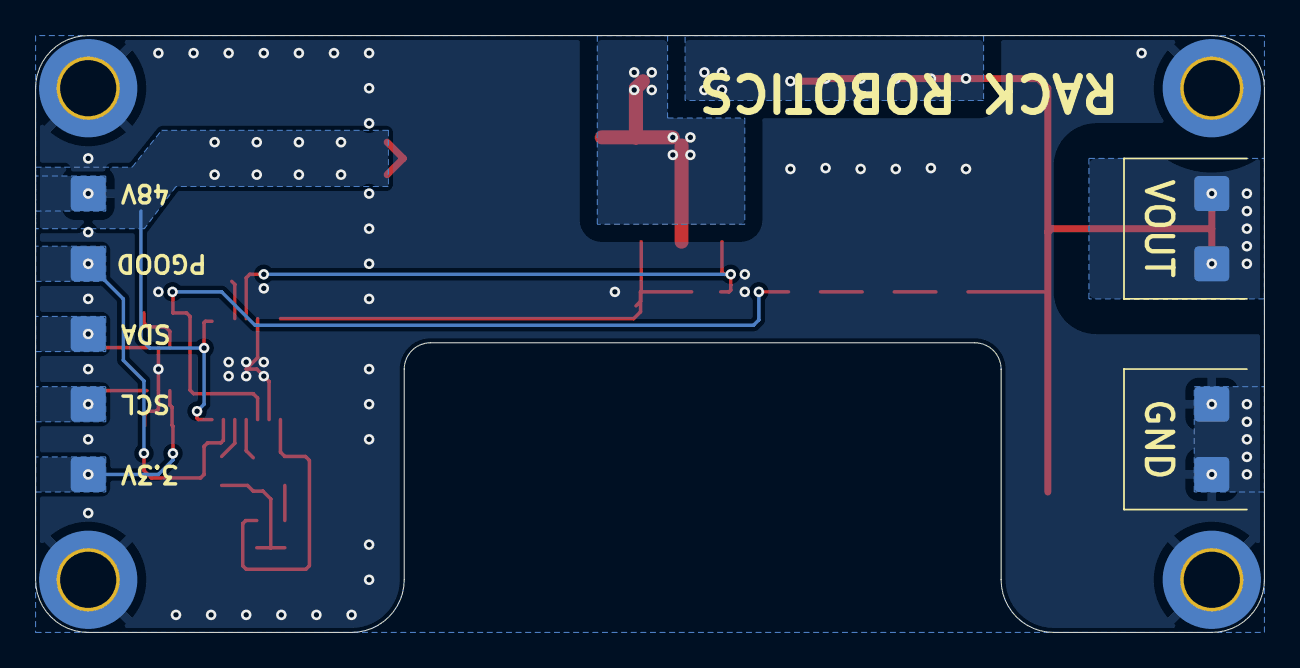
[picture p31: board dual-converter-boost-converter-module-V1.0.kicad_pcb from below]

Board: 4 copper layers, 70.0 x 34.0 mm, 52 parts (9 on the bottom side), 19 nets.

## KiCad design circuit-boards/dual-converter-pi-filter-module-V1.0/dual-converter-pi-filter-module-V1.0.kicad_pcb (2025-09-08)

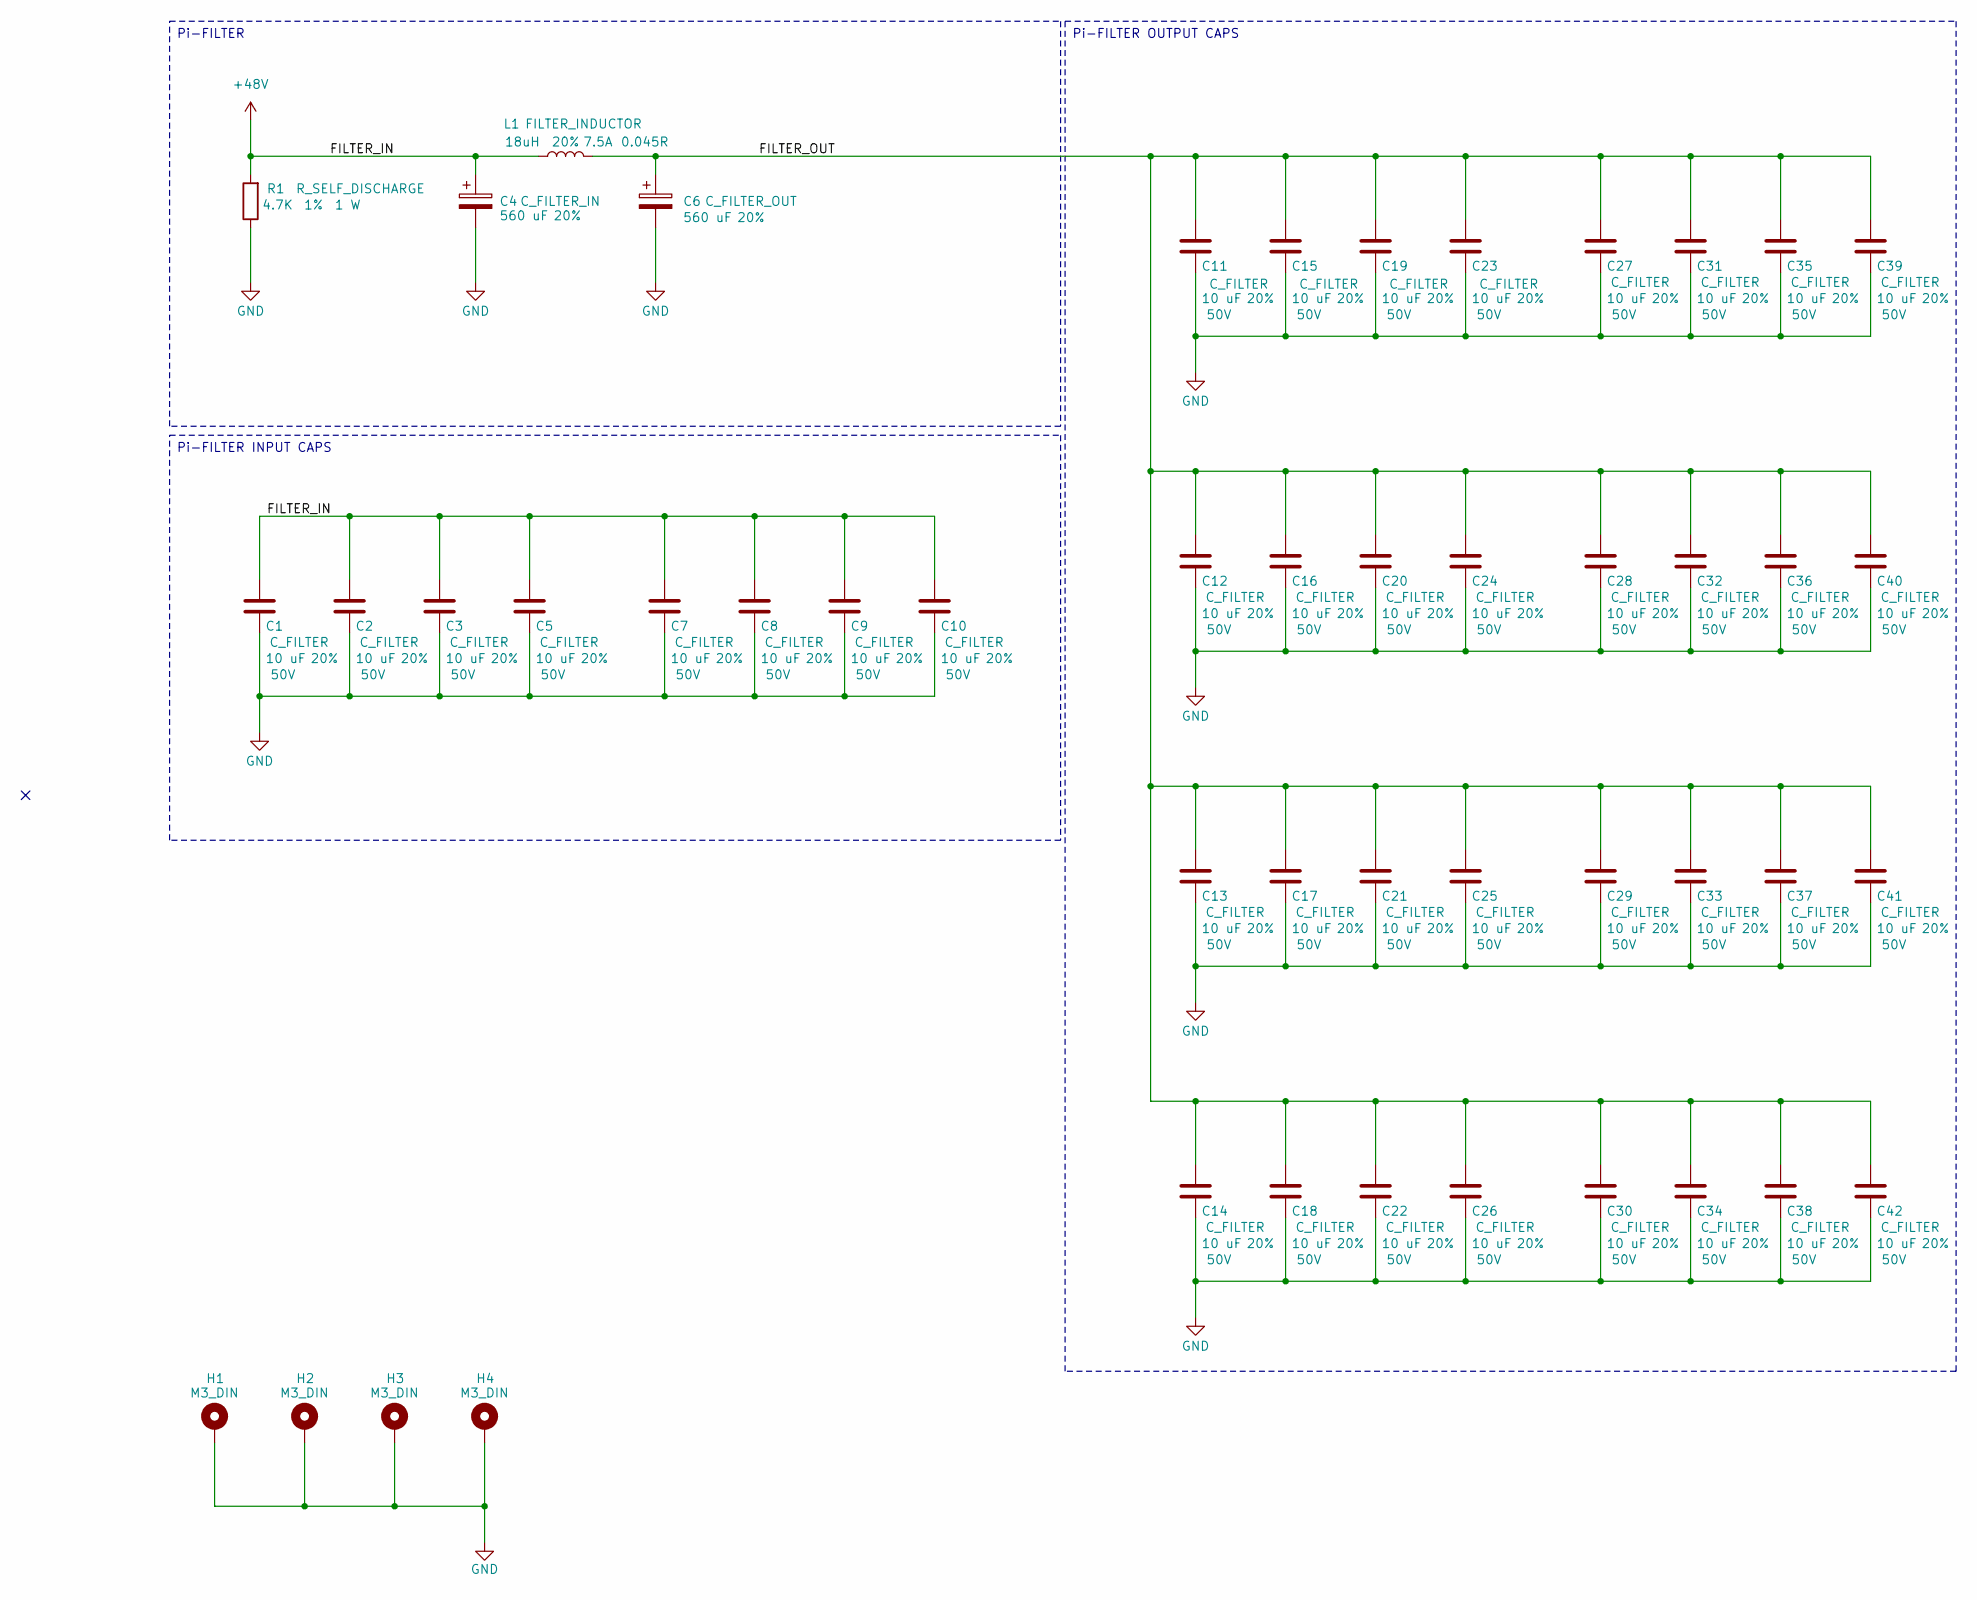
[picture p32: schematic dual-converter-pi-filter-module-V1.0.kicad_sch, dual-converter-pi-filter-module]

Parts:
C1, C2, C3, C5, C7, C8, C9, C10, C11, C12, C13, C14, C15, C16, C17, C18, C19, C20, C21, C22, C23, C24, C25, C26, C27, C28, C29, C30, C31, C32, C33, C34, C35, C36, C37, C38, C39, C40, C41, C42: 10 uF; C_1206_3216Metric; Tolerance 20%; Max Voltage 50V; Manufacturer# CL31A106MBHNNNE; LCSC Part # C96600
C4, C6: 560 uF; PHA225; Tolerance 20%; Manufacturer# PHA225MLP3560QE4; LCSC Part # C3274794
H1, H2, H3, H4: M3_DIN; MountingHole_3.2mm_M3_DIN965_Pad_TopBottom; Manufacturer# NULL
L1: 18uH; SRP1245A; Tolerance 20%; Current Rating 7.5A; Manufacturer# SRP1245A-180M; LCSC Part # C5926042
R1: 4.7K; R_2512_6332Metric; Tolerance 1%; Manufacturer# RC2512JK-074K7L; LCSC Part # C878291

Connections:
+48V: C1.1, C2.1, C3.1, C4.1, C5.1, C7.1, C8.1, C9.1, C10.1, L1.1, R1.2
/FILTER_OUT: C6.1, C11.1, C12.1, C13.1, C14.1, C15.1, C16.1, C17.1, C18.1, C19.1, C20.1, C21.1, C22.1, C23.1, C24.1, C25.1, C26.1, C27.1, C28.1, C29.1, C30.1, C31.1, C32.1, C33.1, C34.1, C35.1, C36.1, C37.1, C38.1, C39.1, C40.1, C41.1, C42.1, L1.2
GND: C1.2, C2.2, C3.2, C4.2, C5.2, C6.2, C7.2, C8.2, C9.2, C10.2, C11.2, C12.2, C13.2, C14.2, C15.2, C16.2, C17.2, C18.2, C19.2, C20.2, C21.2, C22.2, C23.2, C24.2, C25.2, C26.2, C27.2, C28.2, C29.2, C30.2, C31.2, C32.2, C33.2, C34.2, C35.2, C36.2, C37.2, C38.2, C39.2, C40.2, C41.2, C42.2, H1.1, H2.1, H3.1, H4.1, R1.1

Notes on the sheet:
Pi-FILTER INPUT CAPS
Pi-FILTER
Pi-FILTER OUTPUT CAPS

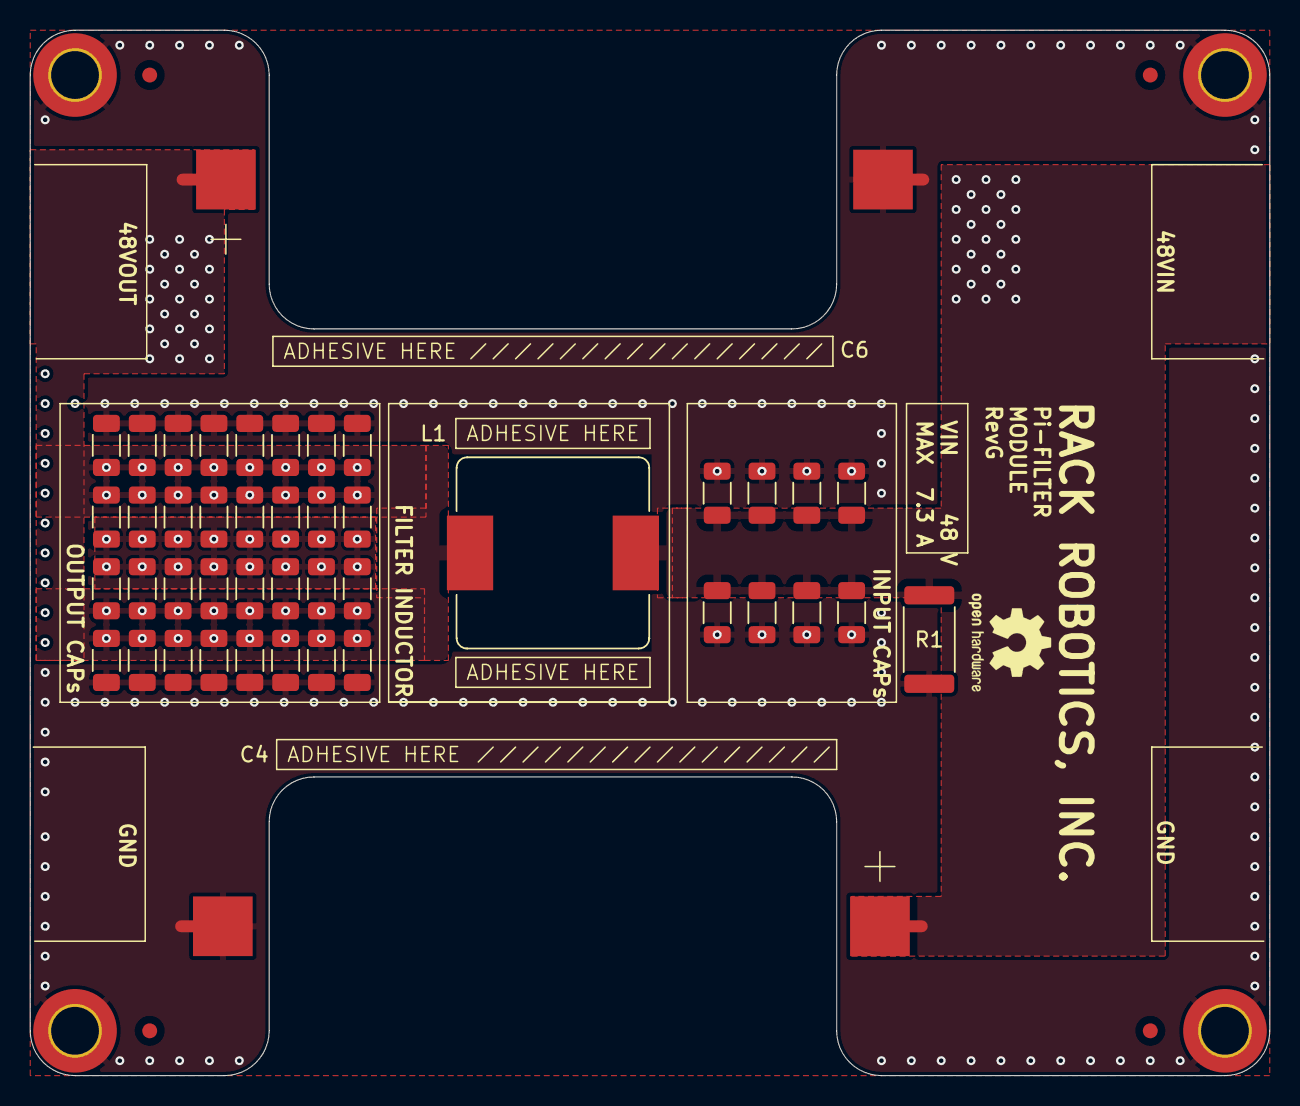
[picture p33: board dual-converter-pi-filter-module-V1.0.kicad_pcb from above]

Board: 4 copper layers, 83.0 x 70.0 mm, 48 parts (0 on the bottom side), 3 nets.

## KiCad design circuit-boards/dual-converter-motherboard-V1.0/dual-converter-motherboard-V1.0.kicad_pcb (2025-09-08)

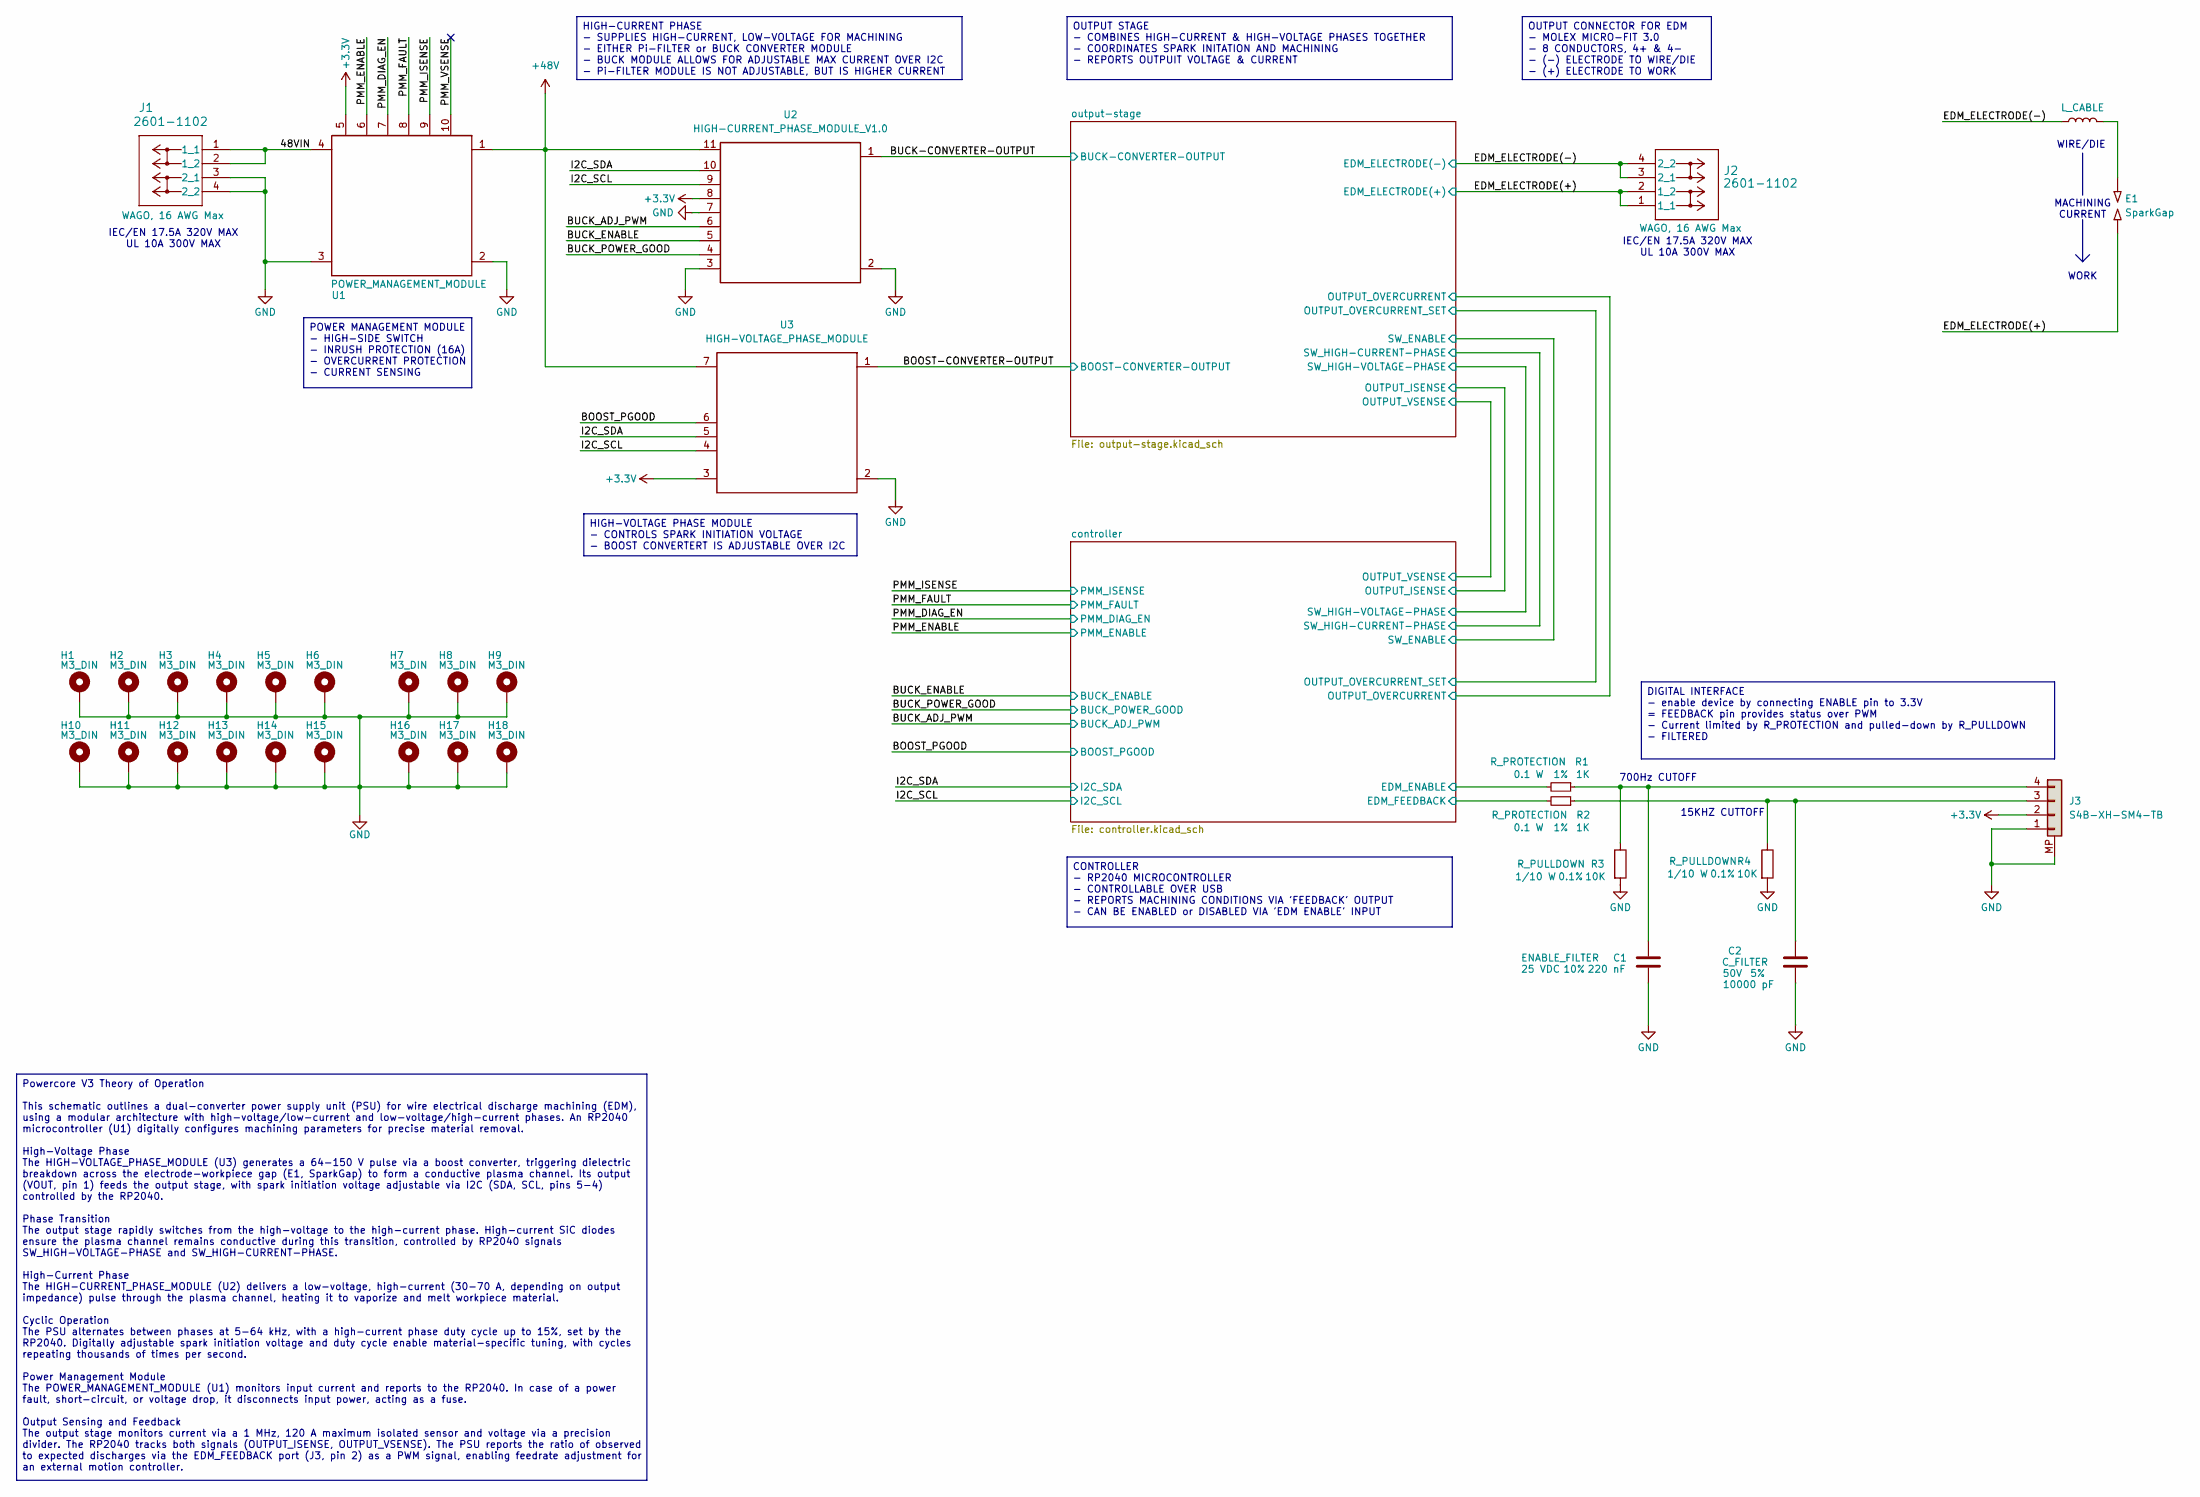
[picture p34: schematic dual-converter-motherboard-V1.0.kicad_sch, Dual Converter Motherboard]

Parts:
C1: 220 nF; C_0603_1608Metric; Tolerance 10%; Max Voltage 25 VDC; Manufacturer# AC0603KRX7R9BB224; LCSC Part # C726565
C2: 10000 pF; C_0603_1608Metric; Tolerance 5%; Max Voltage 50V; Manufacturer# CC0603JRX7R9BB103; LCSC Part # C115056
E1: SparkGap; NULL; Manufacturer# NULL; LCSC Part # NULL
H1, H2, H3, H4, H5, H6, H7, H8, H9, H10, H11, H12, H13, H14, H15, H16, H17, H18: M3_DIN; MountingHole_3.2mm_M3_DIN965_Pad_TopBottom; Manufacturer# NULL
J1, J2: 2601-1102; Manufacturer# 2601-1102; LCSC Part # C7509568
J3: S4B-XH-SM4-TB; Manufacturer# S4B-XH-SM4-TB; LCSC Part # C161861
L_CABLE1: L_CABLE
R1, R2: 1K; R_0603_1608Metric; Tolerance 1%; Manufacturer# RC0603FR-071KL; LCSC Part # C22548
R3, R4: 10K; R_0603_1608Metric; Tolerance 0.1%; Manufacturer# RC0603BR-0710KL; LCSC Part # C20161635
U1: POWER_MANAGEMENT_MODULE; POWER_MANAGEMENT_MODULE_FOOTPRINT_V1.0
U2: HIGH-CURRENT_PHASE_MODULE_V1.0; HIGH-CURRENT_PHASE_MODULE_FOOTPRINT_V1.0
U3: HIGH-VOLTAGE_PHASE_MODULE; HIGH-VOLTAGE_PHASE_MODULE_FOOTPRINT_V1.0

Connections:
+3.3V: J3.2, U1.5, U2.8 (3.3VIN), U3.3 (GND); also elsewhere on the board
+48V: U1.1 (VOUT), U2.11 (48VIN), U3.7 (48VIN); also elsewhere on the board
/48VIN: J1.1 (1_1), J1.2 (1_2), U1.4 (VIN)
/BOOST-CONVERTER-OUTPUT: U3.1 (VOUT); also elsewhere on the board
/BOOST_PGOOD: U3.6 (PGOOD); also elsewhere on the board
/BUCK-CONVERTER-OUTPUT: U2.1 (VOUT); also elsewhere on the board
/BUCK_ADJ_PWM: U2.6 (PWM_ADJ); also elsewhere on the board
/BUCK_ENABLE: U2.5 (ENABLE); also elsewhere on the board
/BUCK_POWER_GOOD: U2.4 (PGOOD); also elsewhere on the board
/EDM_ELECTRODE(+): E1.1, J2.1 (1_1), J2.2 (1_2); also elsewhere on the board
/EDM_ELECTRODE(-): J2.3 (2_1), J2.4 (2_2), L_CABLE1.1; also elsewhere on the board
/I2C_SCL: U2.9 (SCL), U3.4 (SCL); also elsewhere on the board
/I2C_SDA: U2.10 (SDA), U3.5 (SDA); also elsewhere on the board
/PMM_DIAG_EN: U1.7; also elsewhere on the board
/PMM_ENABLE: U1.6; also elsewhere on the board
/PMM_FAULT: U1.8; also elsewhere on the board
/PMM_ISENSE: U1.9; also elsewhere on the board
/PMM_VSENSE: U1.10
/PMM_VSENSE_1: U1.10
/controller/EDM_ENABLE: R1.2; also elsewhere on the board
/controller/EDM_FEEDBACK: R2.2; also elsewhere on the board
GND: C1.2, C2.2, H1.1, H2.1, H3.1, H4.1, H5.1, H6.1, H7.1, H8.1, H9.1, H10.1, H11.1, H12.1, H13.1, H14.1, H15.1, H16.1, H17.1, H18.1, J1.3 (2_1), J1.4 (2_2), J3.1, J3.MP, R3.2, R4.2, U1.2, U1.3, U2.2 (GND), U2.3 (GND), U2.7 (GND), U3.2 (GND); also elsewhere on the board
unnamed: E1.2, L_CABLE1.2
unnamed: C2.1, J3.3, R2.1, R4.1
unnamed: C1.1, J3.4, R1.1, R3.1

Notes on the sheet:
IEC/EN 17.5A 320V MAX UL 10A 300V MAX
WORK
700Hz CUTOFF
MACHINING CURRENT
WIRE/DIE
15KHZ CUTTOFF
CONTROLLER - RP2040 MICROCONTROLLER - CONTROLLABLE OVER USB - REPORTS MACHINING CONDITIONS VIA 'FEEDBACK' OUTPUT - CAN BE ENABLED or DISABLED VIA 'EDM ENABLE' INPUT
HIGH-VOLTAGE PHASE MODULE - CONTROLS SPARK INITIATION VOLTAGE - BOOST CONVERTERT IS ADJUSTABLE OVER I2C
OUTPUT CONNECTOR FOR EDM - MOLEX MICRO-FIT 3.0 - 8 CONDUCTORS, 4+ & 4- - (-) ELECTRODE TO WIRE/DIE - (+) ELECTRODE TO WORK
HIGH-CURRENT PHASE - SUPPLIES HIGH-CURRENT, LOW-VOLTAGE FOR MACHINING - EITHER Pi-FILTER or BUCK CONVERTER MODULE - BUCK MODULE ALLOWS FOR ADJUSTABLE MAX CURRENT OVER I2C - Pi-FILTER MODULE IS NOT ADJUSTABLE, BUT IS HIGHER CURRENT
Powercore V3 Theory of Operation This schematic outlines a dual-converter power supply unit (PSU) for wire electrical discharge machining (EDM), using a modular architecture with high-voltage/low-current and low-voltage/high-current phases. An RP2040 microcontroller (U1) digitally configures machin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
OUTPUT STAGE - COMBINES HIGH-CURRENT & HIGH-VOLTAGE PHASES TOGETHER - COORDINATES SPARK INITATION AND MACHINING - REPORTS OUTPUIT VOLTAGE & CURRENT
POWER MANAGEMENT MODULE - HIGH-SIDE SWITCH - INRUSH PROTECTION (16A) - OVERCURRENT PROTECTION - CURRENT SENSING
DIGITAL INTERFACE - enable device by connecting ENABLE pin to 3.3V = FEEDBACK pin provides status over PWM - Current limited by R_PROTECTION and pulled-down by R_PULLDOWN - FILTERED

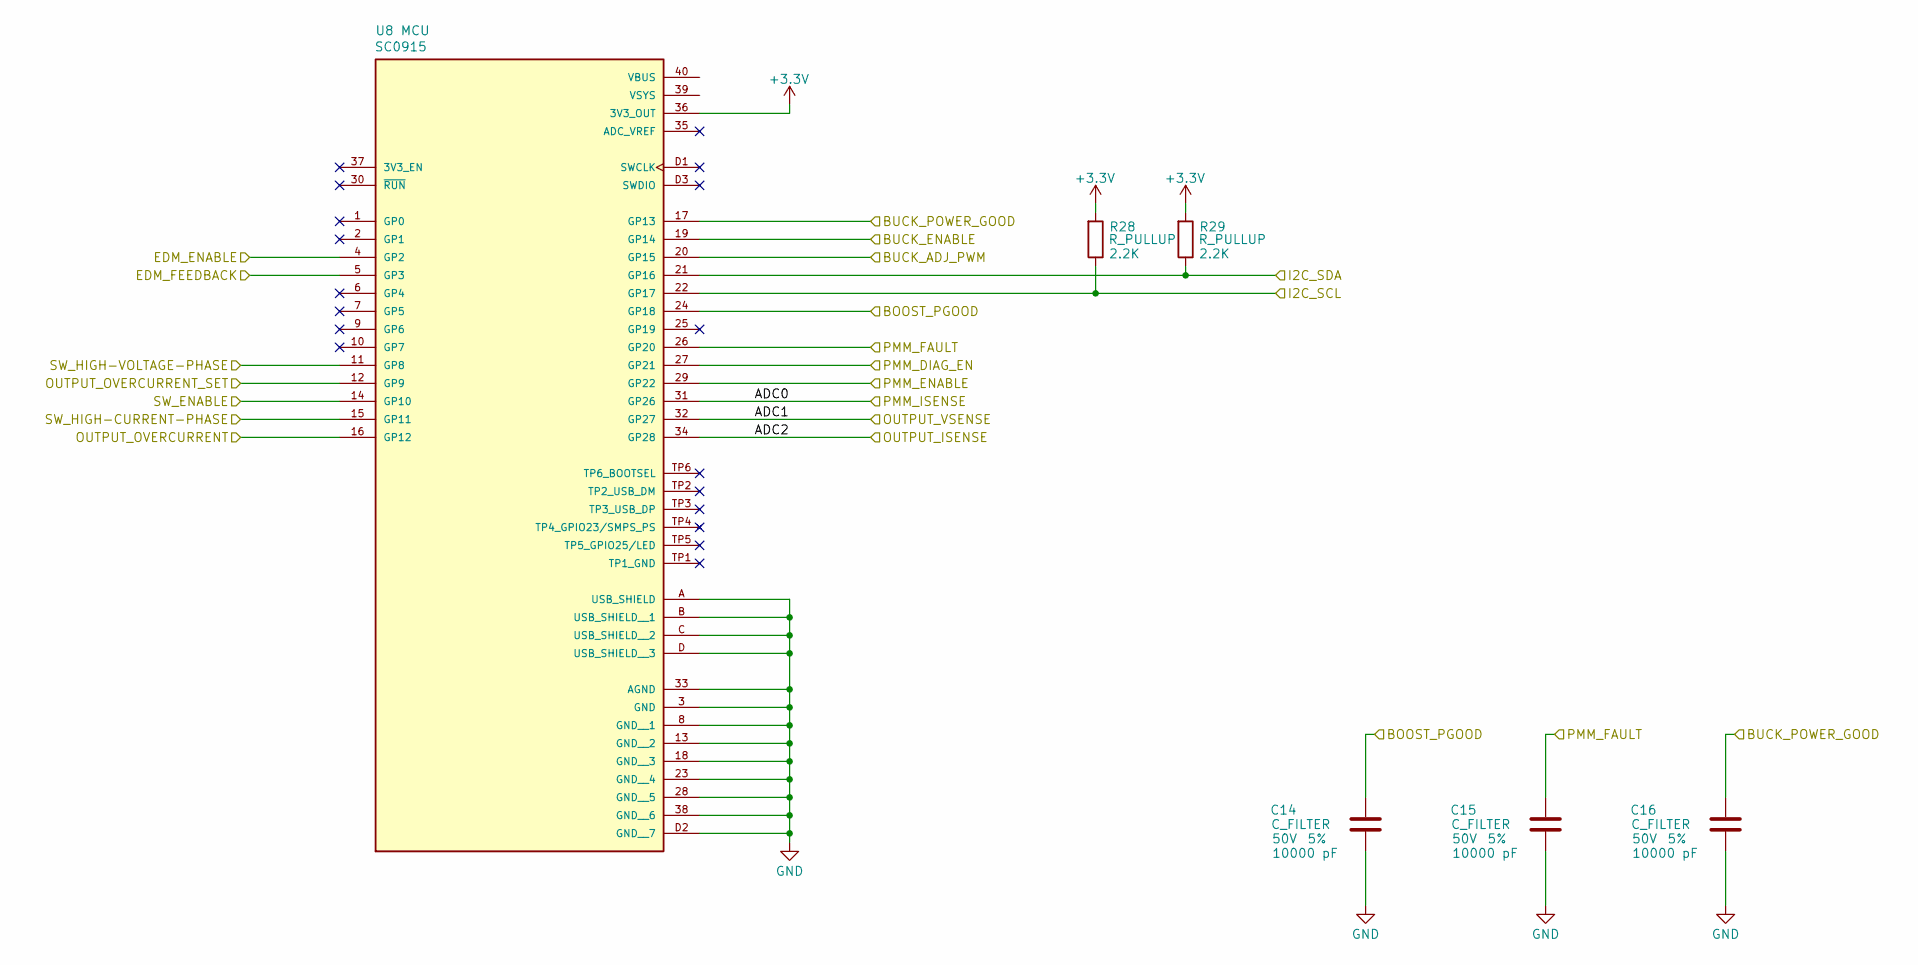
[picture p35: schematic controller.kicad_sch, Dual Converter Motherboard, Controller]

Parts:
C14, C15, C16: 10000 pF; C_0603_1608Metric; Tolerance 5%; Max Voltage 50V; Manufacturer# CC0603JRX7R9BB103; LCSC Part # C115056
R28, R29: 2.2K; R_0603_1608Metric; Tolerance 1%; Manufacturer# RC0603FR-132K2L; LCSC Part # C3032396
U8: SC0915; Manufacturer# SC0915; LCSC Part # C7203002

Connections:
+3.3V: R28.2, R29.2, U8.36 (3V3_OUT); also elsewhere on the board
/BOOST_PGOOD: C14.1, U8.24 (GP18); also elsewhere on the board
/BUCK_ADJ_PWM: U8.20 (GP15); also elsewhere on the board
/BUCK_ENABLE: U8.19 (GP14); also elsewhere on the board
/BUCK_POWER_GOOD: C16.1, U8.17 (GP13); also elsewhere on the board
/I2C_SCL: R28.1, U8.22 (GP17); also elsewhere on the board
/I2C_SDA: R29.1, U8.21 (GP16); also elsewhere on the board
/PMM_DIAG_EN: U8.27 (GP21); also elsewhere on the board
/PMM_ENABLE: U8.29 (GP22); also elsewhere on the board
/PMM_FAULT: C15.1, U8.26 (GP20); also elsewhere on the board
/PMM_ISENSE: U8.31 (GP26); also elsewhere on the board
/controller/ADC1: U8.32 (GP27); also elsewhere on the board
/controller/ADC2: U8.34 (GP28); also elsewhere on the board
/controller/EDM_ENABLE: U8.4 (GP2); also elsewhere on the board
/controller/EDM_FEEDBACK: U8.5 (GP3); also elsewhere on the board
/controller/OUTPUT_OVERCURRENT: U8.16 (GP12); also elsewhere on the board
/controller/OUTPUT_OVERCURRENT_SET: U8.12 (GP9); also elsewhere on the board
/controller/SW_ENABLE: U8.14 (GP10); also elsewhere on the board
/controller/SW_HIGH-CURRENT-PHASE: U8.15 (GP11); also elsewhere on the board
/controller/SW_HIGH-VOLTAGE-PHASE: U8.11 (GP8); also elsewhere on the board
GND: C14.2, C15.2, C16.2, U8.3 (GND), U8.8 (GND__1), U8.13 (GND__2), U8.18 (GND__3), U8.23 (GND__4), U8.28 (GND__5), U8.33 (AGND), U8.38 (GND__6), U8.A (USB_SHIELD), U8.B (USB_SHIELD__1), U8.C (USB_SHIELD__2), U8.D (USB_SHIELD__3), U8.D2 (GND__7); also elsewhere on the board

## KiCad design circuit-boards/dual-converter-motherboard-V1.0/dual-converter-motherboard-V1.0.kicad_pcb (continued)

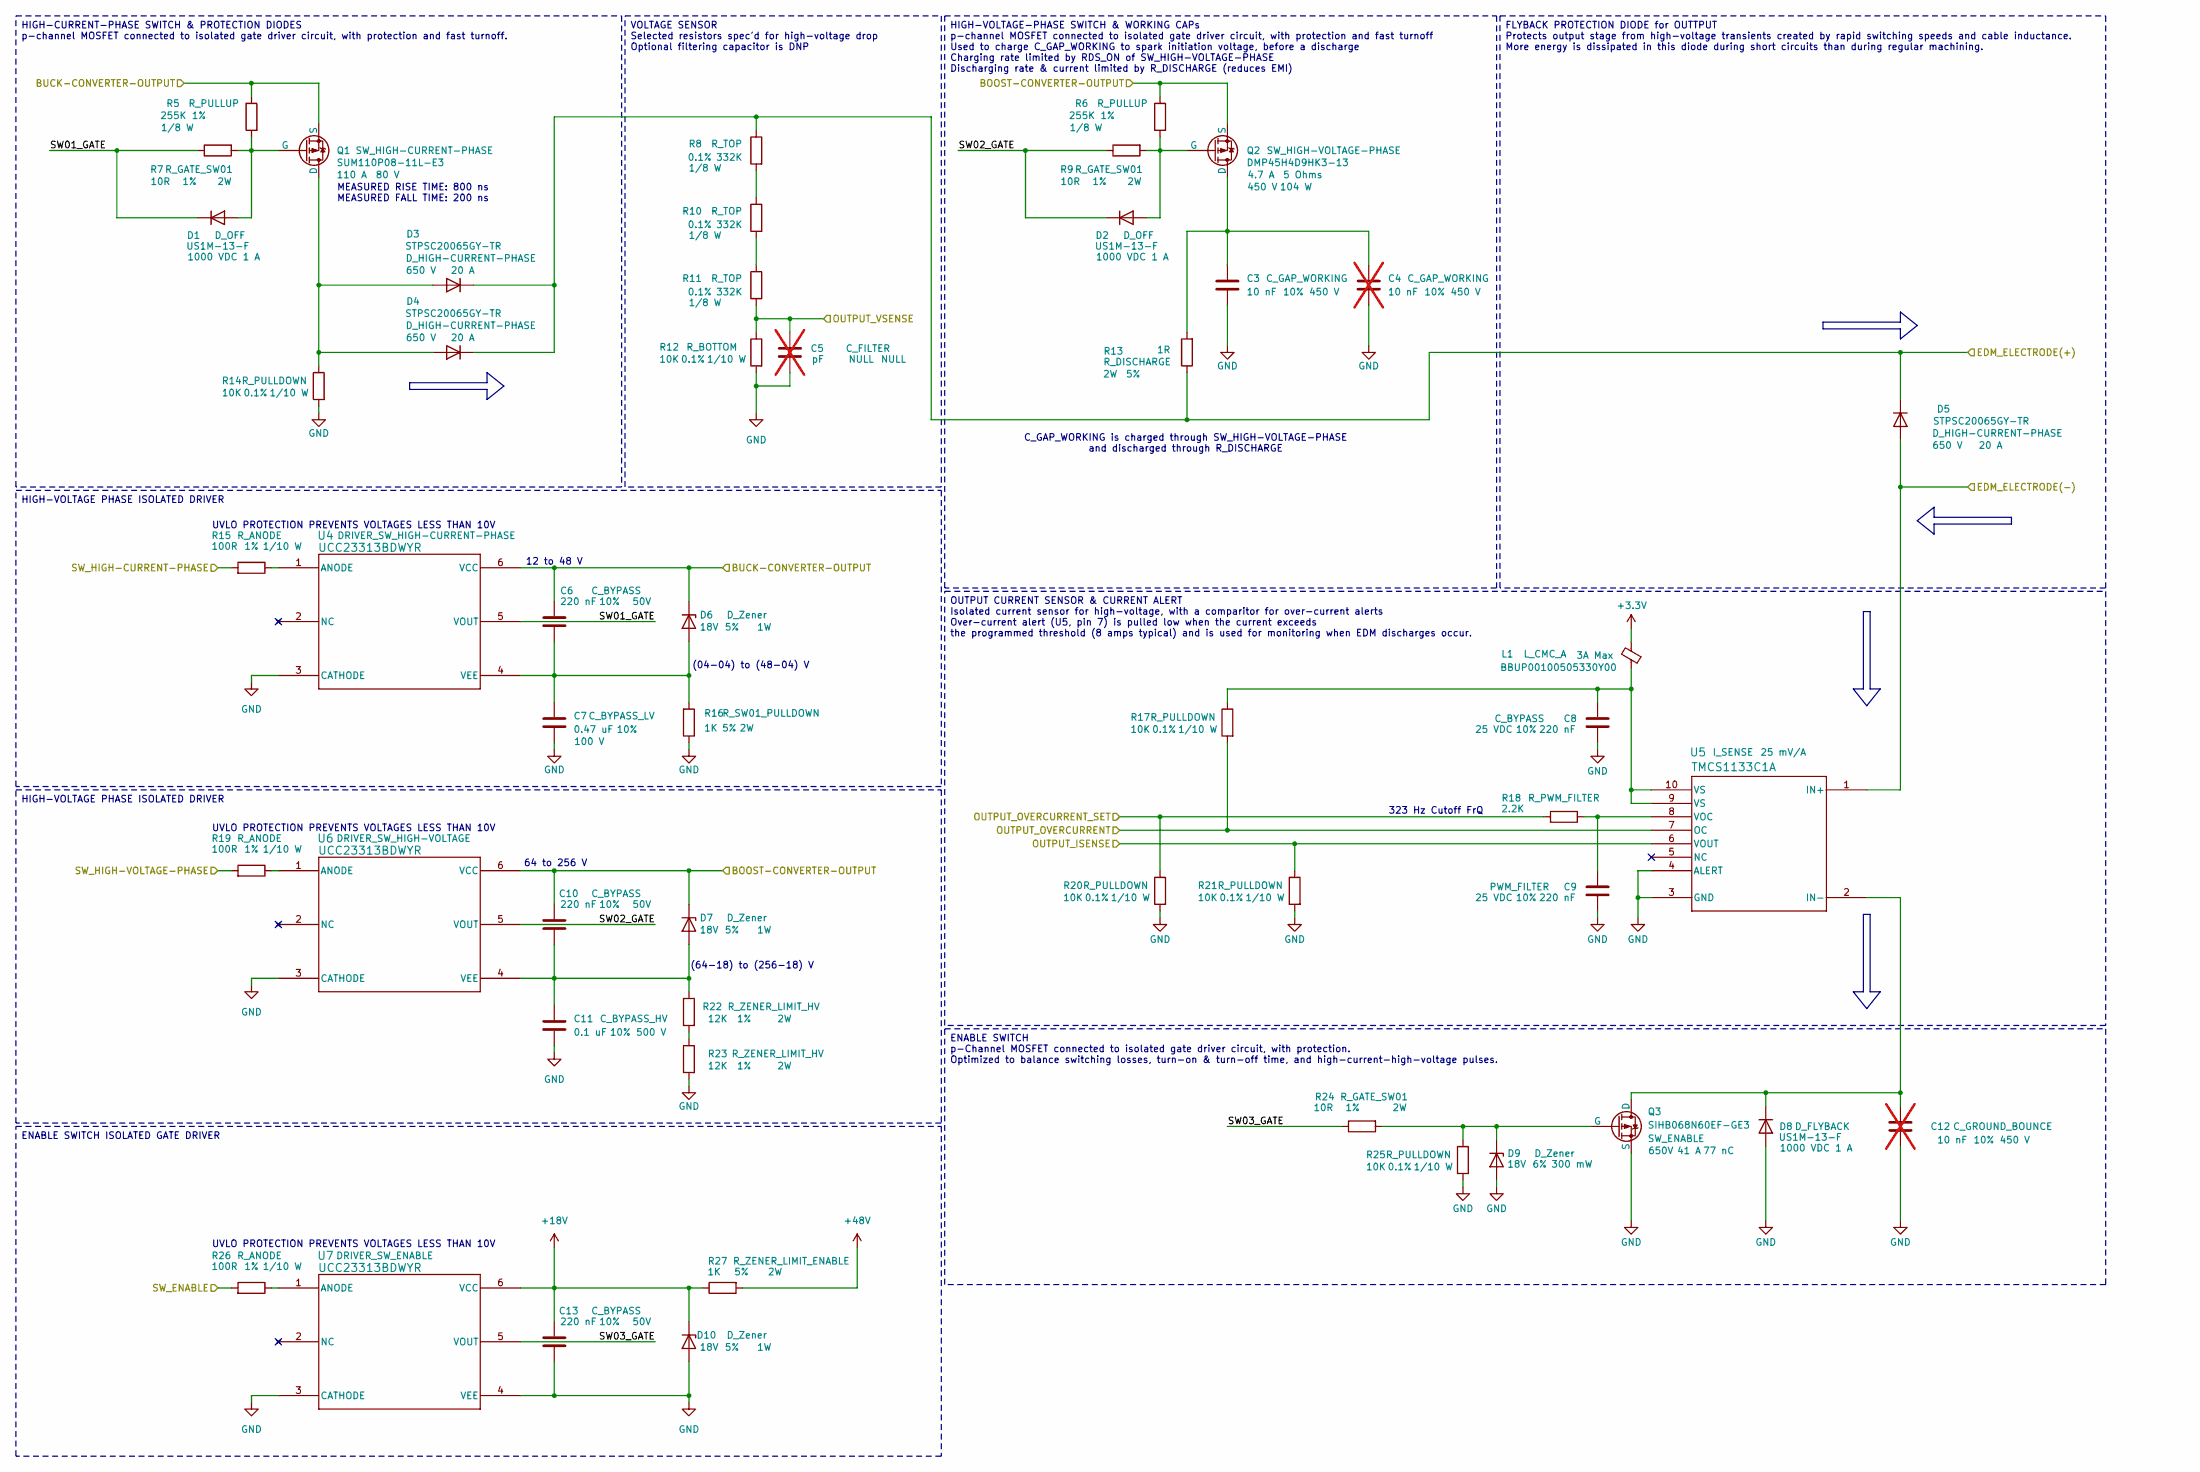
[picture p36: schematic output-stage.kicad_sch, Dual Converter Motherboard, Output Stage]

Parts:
C3: 10 nF; C_0805_2012Metric; Tolerance 10%; Max Voltage 450 V; Manufacturer# C2012X7T2W103K085AA; LCSC Part # C342860
C4, C12: 10 nF; C_0805_2012Metric; Tolerance 10%; Max Voltage 450 V; Manufacturer# C2012X7T2W103K085AA; LCSC Part # C342860; not fitted
C5: pF; C_0603_1608Metric; Tolerance NULL; Max Voltage NULL; Manufacturer# NULL; LCSC Part # NULL; not fitted
C6, C10, C13: 220 nF; C_0603_1608Metric; Tolerance 10%; Max Voltage 50V; Manufacturer# AC0603KRX7R9BB224; LCSC Part # C726565
C7: 0.47 uF; C_0805_2012Metric; Tolerance 10%; Max Voltage 100 V; Manufacturer# CC0805KKX7R0BB474; LCSC Part # C596323
C8, C9: 220 nF; C_0603_1608Metric; Tolerance 10%; Max Voltage 25 VDC; Manufacturer# AC0603KRX7R9BB224; LCSC Part # C726565
C11: 0.1 uF; C_1210_3225Metric; Tolerance 10%; Max Voltage 500 V; Manufacturer# C1210C104KCRACTU; LCSC Part # C141218
D1, D2, D8: US1M-13-F; D_SMA; Tolerance NULL; Manufacturer# US1M-13-F; LCSC Part # C99333
D3, D4, D5: STPSC20065GY-TR; Tolerance NULL; Manufacturer# STPSC20065GY-TR; LCSC Part # C2965441
D6, D7, D10: D_Zener; D_SMA; Zener Voltage 18V; Tolerance 5%; Manufacturer# SMAZ18-13-F; LCSC Part # C110525
D9: D_Zener; D_SOD-323; Zener Voltage 18V; Tolerance 6%; Manufacturer# MM3Z18VT1G; LCSC Part # C82043
L1: BBUP00100505330Y00; L_0402_1005Metric; Manufacturer# BLM15AX100SN1D; LCSC Part # C668299
Q1: SUM110P08-11L-E3; Max Voltage 80 V; Manufacturer# SUM110P08-11L-E3; LCSC Part # C2838509
Q2: DMP45H4D9HK3-13; Max Voltage 450 V; Manufacturer# DMP45H4D9HK3-13
Q3: SIHB068N60EF-GE3; TO-263-2; Max Voltage 650V; Manufacturer# SIHB068N60EF-GE3; LCSC Part # C3009875
R5, R6: 255K; R_0603_1608Metric; Tolerance 1%; Manufacturer# RC0603FR-07255KL; LCSC Part # C295887
R7, R9, R24: 10R; R_2512_6332Metric; Tolerance 1%; Manufacturer# SR2512JK-7W10RL
R8, R10, R11: 332K; R_0805_2012Metric; Tolerance 0.1%; Manufacturer# RT0805BRD07332KL
R12, R14, R17, R20, R21, R25: 10K; R_0603_1608Metric; Tolerance 0.1%; Manufacturer# RC0603BR-0710KL; LCSC Part # C20161635
R13: 1R; R_2512_6332Metric; Tolerance 5%; Manufacturer# CRM2512-JW-1R0ELF; LCSC Part # C840599
R15, R19, R26: 100R; R_0603_1608Metric; Tolerance 1%; Manufacturer# RC0603FR-10100RL; LCSC Part # C20161635
R16, R27: 1K; R_2512_6332Metric; Tolerance 5%; Manufacturer# RES 1K OHM 5% 2W 2512; LCSC Part # C7038808
R18: 2.2K; R_0603_1608Metric; Tolerance 1%; Manufacturer# RC0603FR-132K2L; LCSC Part # C3032396
R22, R23: 12K; R_2512_6332Metric; Tolerance 1%; Manufacturer# CRGP2512F12K; LCSC Part # C2082818
U4, U6, U7: UCC23313BDWYR; Tolerance NULL; Manufacturer# UCC23313BDWYR; LCSC Part # C2868027
U5: TMCS1133C1A; TMCS1133C3AQDVGR; Tolerance 1%; Manufacturer# TMCS1133C1AQDVGR; LCSC Part # C32266987

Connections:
+3.3V: L1.2; also elsewhere on the board
+18V: C13.1, D10.1 (K), R27.1, U7.6 (VCC)
+48V: R27.2; also elsewhere on the board
/BOOST-CONVERTER-OUTPUT: C10.1, D7.1 (K), Q2.3 (S), R6.1, U6.6 (VCC); also elsewhere on the board
/BUCK-CONVERTER-OUTPUT: C6.1, D6.1 (K), Q1.3 (S), R5.1, U4.6 (VCC); also elsewhere on the board
/EDM_ELECTRODE(+): D3.1 (K), D4.1 (K), D5.1 (K), R8.1, R13.1; also elsewhere on the board
/EDM_ELECTRODE(-): D5.2 (A), U5.1 (IN+); also elsewhere on the board
/controller/ADC1: C5.1, R11.2, R12.1; also elsewhere on the board
/controller/ADC2: R21.1, U5.6 (VOUT); also elsewhere on the board
/controller/OUTPUT_OVERCURRENT: R17.2, U5.7 (OC); also elsewhere on the board
/controller/OUTPUT_OVERCURRENT_SET: R18.1, R20.1; also elsewhere on the board
/controller/SW_ENABLE: R26.2; also elsewhere on the board
/controller/SW_HIGH-CURRENT-PHASE: R15.2; also elsewhere on the board
/controller/SW_HIGH-VOLTAGE-PHASE: R19.2; also elsewhere on the board
/output-stage/SW01_GATE: D1.1 (K), R7.1, U4.5 (VOUT)
/output-stage/SW02_GATE: D2.1 (K), R9.1, U6.5 (VOUT)
/output-stage/SW03_GATE: R24.1, U7.5 (VOUT)
GND: C3.2, C4.2, C5.2, C7.2, C8.2, C9.2, C11.2, C12.2, C13.2, D8.2 (A), D9.2 (A), D10.2 (A), Q3.3 (S), R12.2, R14.2, R16.1, R20.2, R21.2, R23.2, R25.2, U4.3 (CATHODE), U5.3 (GND), U5.4 (ALERT), U6.3 (CATHODE), U7.3 (CATHODE), U7.4 (VEE); also elsewhere on the board
unnamed: C8.1, L1.1, R17.1, U5.9 (VS), U5.10 (VS)
unnamed: D1.2 (A), Q1.2 (G), R5.2, R7.2
unnamed: D2.2 (A), Q2.2 (G), R6.2, R9.2
unnamed: D3.2 (A), D4.2 (A), Q1.1 (D), R14.1
unnamed: C6.2, C7.1, D6.2 (A), R16.2, U4.4 (VEE)
unnamed: C10.2, C11.1, D7.2 (A), R22.1, U6.4 (VEE)
unnamed: C12.1, D8.1 (K), Q3.2 (D), U5.2 (IN-)
unnamed: D9.1 (K), Q3.1 (G), R24.2, R25.1
unnamed: C3.1, C4.1, Q2.1 (D), R13.2
unnamed: R8.2, R10.1
unnamed: R10.2, R11.1
unnamed: R22.2, R23.1
unnamed: R15.1, U4.1 (ANODE)
unnamed: C9.1, R18.2, U5.8 (VOC)
unnamed: R19.1, U6.1 (ANODE)
unnamed: R26.1, U7.1 (ANODE)

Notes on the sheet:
UVLO PROTECTION PREVENTS VOLTAGES LESS THAN 10V
C_GAP_WORKING is charged through SW_HIGH-VOLTAGE-PHASE and discharged through R_DISCHARGE
323 Hz Cutoff FrQ
(04-04) to (48-04) V
12 to 48 V
(64-18) to (256-18) V
64 to 256 V
MEASURED RISE TIME: 800 ns MEASURED FALL TIME: 200 ns
FLYBACK PROTECTION DIODE for OUTTPUT Protects output stage from high-voltage transients created by rapid switching speeds and cable inductance. More energy is dissipated in this diode during short circuits than during regular machining.
HIGH-VOLTAGE PHASE ISOLATED DRIVER
ENABLE SWITCH ISOLATED GATE DRIVER
ENABLE SWITCH p-Channel MOSFET connected to isolated gate driver circuit, with protection. Optimized to balance switching losses, turn-on & turn-off time, and high-current-high-voltage pulses.
HIGH-VOLTAGE-PHASE SWITCH & WORKING CAPs p-channel MOSFET connected to isolated gate driver circuit, with protection and fast turnoff Used to charge C_GAP_WORKING to spark initiation voltage, before a discharge Charging rate limited by RDS_ON of SW_HIGH-VOLTAGE-PHASE Discharging rate & current limi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
OUTPUT CURRENT SENSOR & CURRENT ALERT Isolated current sensor for high-voltage, with a comparitor for over-current alerts Over-current alert (U5, pin 7) is pulled low when the current exceeds the programmed threshold (8 amps typical) and is used for monitoring when EDM discharges occur.
VOLTAGE SENSOR Selected resistors spec'd for high-voltage drop Optional filtering capacitor is DNP
HIGH-CURRENT-PHASE SWITCH & PROTECTION DIODES p-channel MOSFET connected to isolated gate driver circuit, with protection and fast turnoff.

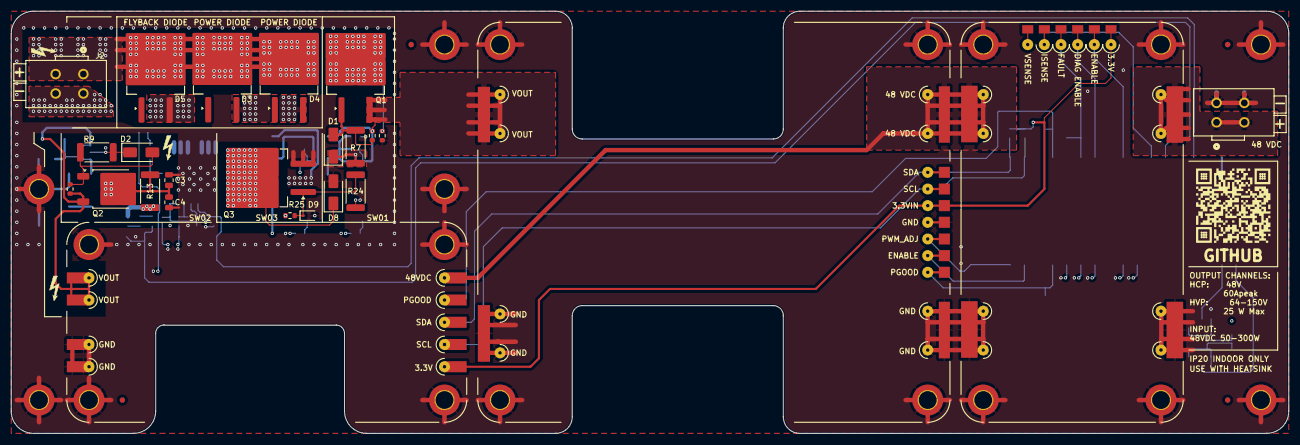
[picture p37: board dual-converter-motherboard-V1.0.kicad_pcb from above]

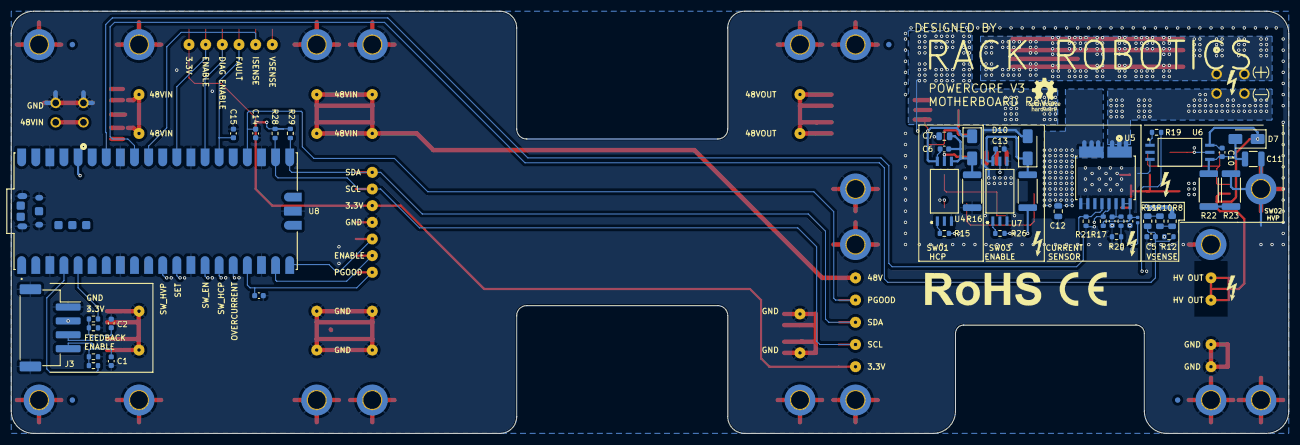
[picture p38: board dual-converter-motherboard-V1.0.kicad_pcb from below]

Board: 6 copper layers, 230.0 x 76.0 mm, 118 parts (45 on the bottom side), 49 nets.

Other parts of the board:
POGO1, POGO2, POGO3, POGO4, POGO5, POGO6, POGO7, POGO8, POGO9, POGO10, POGO11, POGO12, POGO13, POGO14, POGO15, POGO16, POGO17, POGO18, POGO19, POGO20, POGO21, POGO22, POGO23, POGO24, POGO25, POGO26, POGO27, POGO28, POGO29, POGO30: 0906-8-15-20-76-14-11-0

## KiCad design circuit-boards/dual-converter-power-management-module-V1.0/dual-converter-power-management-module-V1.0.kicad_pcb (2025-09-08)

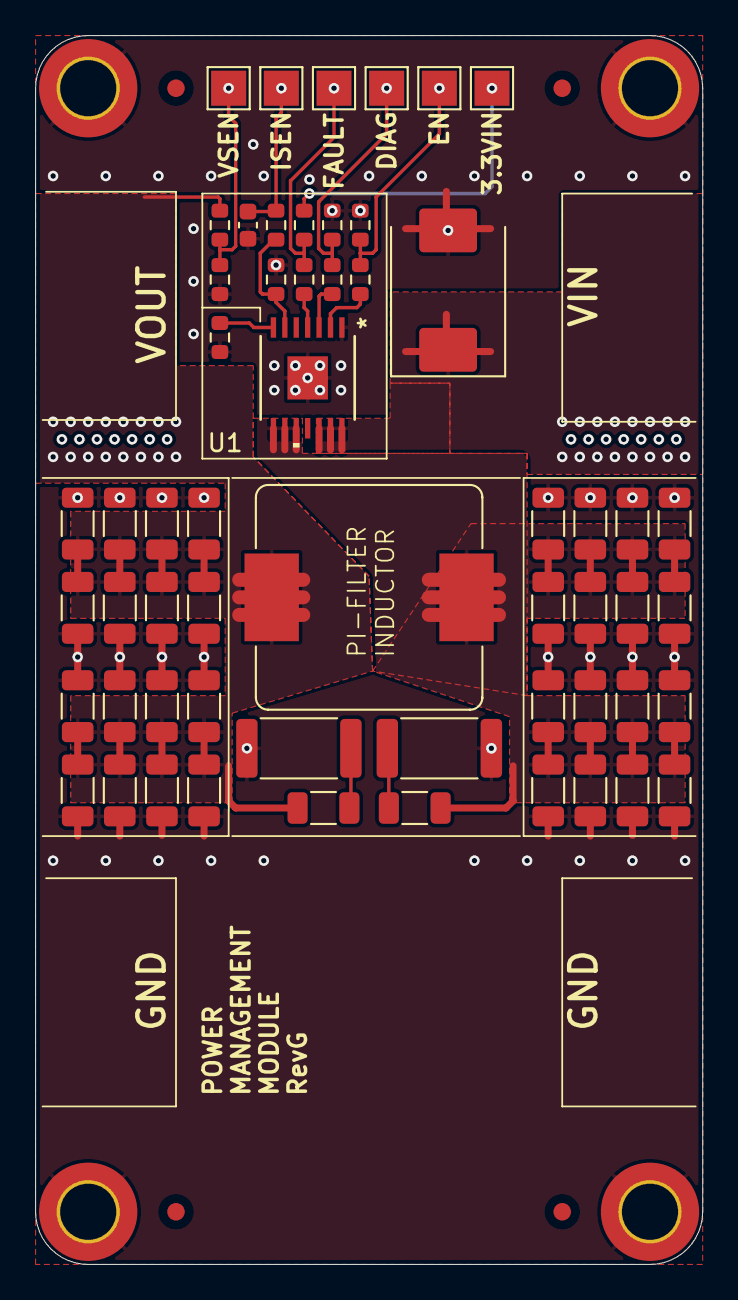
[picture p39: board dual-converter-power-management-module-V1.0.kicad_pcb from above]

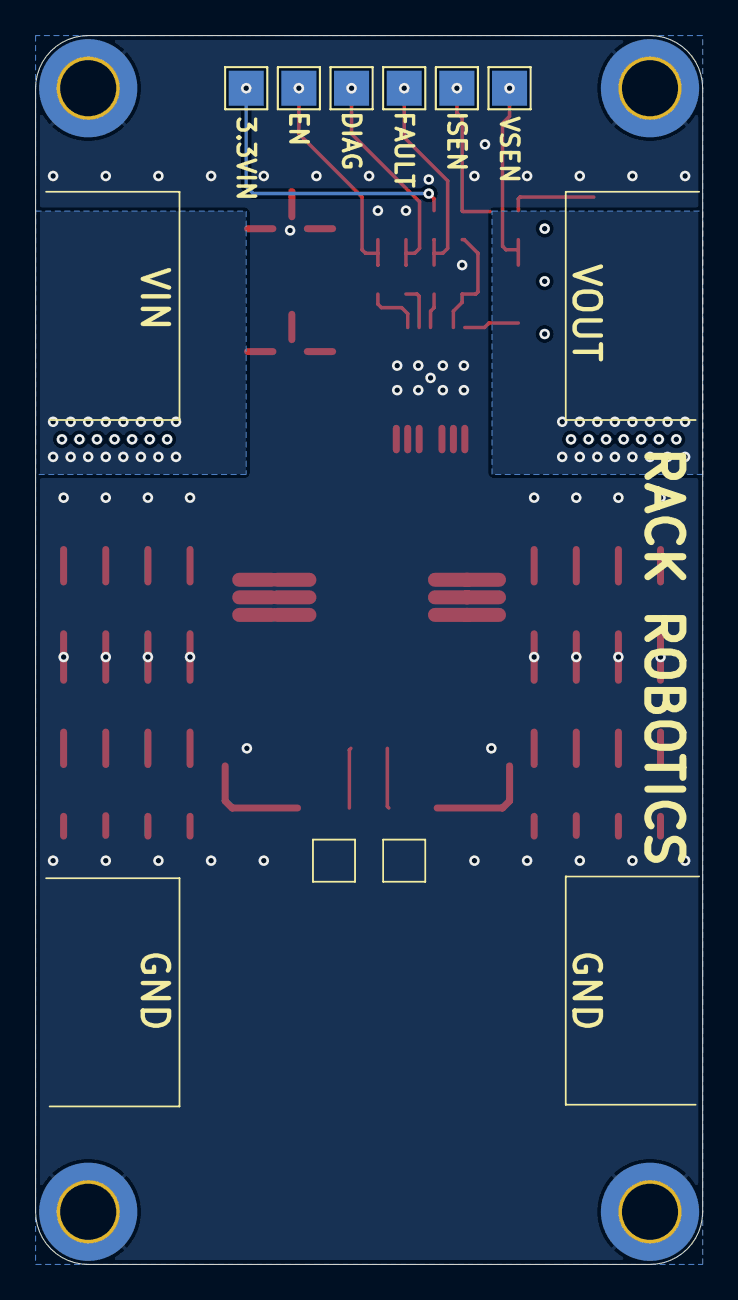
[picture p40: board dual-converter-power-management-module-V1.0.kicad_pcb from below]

Board: 4 copper layers, 38.0 x 70.0 mm, 67 parts (6 on the bottom side), 17 nets.

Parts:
C1: 1 uF; C_0603_1608Metric
C2, C3, C4, C5, C6, C7, C8, C9, C10, C11, C12, C13, C14, C15, C16, C17, C18, C19, C20, C21, C22, C23, C24, C25, C26, C27, C28, C29, C30, C31, C32, C33, C34, C35: 10 uF; C_1206_3216Metric
D1: SMCJ60A-E3/57T; D_SMC
H1, H2, H3, H4: M3_DIN; MountingHole_3.2mm_M3_DIN965_Pad_TopBottom
L1: 18uH; SRP1245A
R1, R6, R7: 100K; R_0603_1608Metric
R2, R3, R4, R5: 2.2K; R_0603_1608Metric
R8: 249R; R_0603_1608Metric
R9: 0R; R_0603_1608Metric
R10, R13: 1R; R_2512_6332Metric
R11: 172K; R_0603_1608Metric
R12: 10K; R_0603_1608Metric
TP1, TP2: 3.3VIN; TestPoint_Pad_2.0x2.0mm
TP3, TP4: ENABLE; TestPoint_Pad_2.0x2.0mm
TP5, TP6: DIAG_EN; TestPoint_Pad_2.0x2.0mm
TP7, TP10: FAULT; TestPoint_Pad_2.0x2.0mm
TP11, TP12: ISENSE; TestPoint_Pad_2.0x2.0mm
TP13, TP14: VSENSE_VIN; TestPoint_Pad_2.0x2.0mm
U1: TPS1HTC30AQPWPRQ1; TPS1HTC30-Q1

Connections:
+3.3V: R1.1, TP1.1, TP2.1
+48V: C19.1, C20.1, C21.1, C22.1, C23.1, C24.1, C25.1, C26.1, C27.1, C28.1, C29.1, C30.1, C31.1, C32.1, C33.1, C34.1, C35.1, L1.2, R11.1
+48VIN: D1.1 (A1), U1.12 (VS), U1.13 (VS), U1.14 (VS)
/FILTER_IN: C2.1, C3.1, C4.1, C5.1, C6.1, C7.1, C8.1, C9.1, C10.1, C11.1, C12.1, C13.1, C14.1, C15.1, C16.1, C17.1, C18.1, L1.1, U1.8 (VOUT), U1.9 (VOUT), U1.10 (VOUT)
/VSENSE_VIN: R11.2, R12.1, TP13.1, TP14.1
GND: C1.2, C2.2, C3.2, C4.2, C5.2, C6.2, C7.2, C8.2, C9.2, C11.2, C12.2, C13.2, C14.2, C15.2, C16.2, C17.2, C18.2, C19.2, C20.2, C21.2, C22.2, C23.2, C24.2, C25.2, C26.2, C28.2, C29.2, C30.2, C31.2, C32.2, C33.2, C34.2, C35.2, D1.2 (A2), H1.1, H2.1, H3.1, H4.1, R6.2, R7.2, R8.2, R9.2, R10.2, R12.2, R13.2, U1.1 (GND)
unnamed: C1.1, R5.1, TP11.1, TP12.1
unnamed: C10.2, R10.1
unnamed: C27.2, R13.1
unnamed: R1.2, R4.1, TP7.1, TP10.1
unnamed: R2.1, R6.1, TP3.1, TP4.1
unnamed: R3.1, R7.1, TP5.1, TP6.1
unnamed: R4.2, U1.4 (*FAULT)
unnamed: R3.2, U1.3 (DIAG_EN)
unnamed: R2.2, U1.2 (EN)
unnamed: R9.1, U1.7 (ILIM)
unnamed: R5.2, R8.1, U1.6 (SNS)

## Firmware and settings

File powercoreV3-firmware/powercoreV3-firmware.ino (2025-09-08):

//Rack Robotics, Inc.
//Powercore Development Firmware
//For use with Rarduino-Pico Plugin by EarlePhilhower
//Copyright (c) 2025 Rack Robotics, Inc. All rights reserved.
//This firmware is for Powercore hardware revision F & G

// Software Version
const String SOFTWARE_VERSION = "1.1.0-beta";

//=============================================================================
// INCLUDES
//=============================================================================
#include <stdio.h>
#include <string.h>
#include <stdlib.h>
#include <ctype.h> 
#include "pico/stdlib.h"
#include "hardware/irq.h"
#include "hardware/gpio.h"
#include "hardware/timer.h"
#include "hardware/adc.h"
#include "hardware/pwm.h"
#include "hardware/i2c.h"

//=============================================================================
// ENUMERATIONS
//=============================================================================
// Device States
enum DeviceState {
    STARTUP,                            // Device is in startup state
    PERIPHERAL_MANAGEMENT,              // Device is in peripheral management state
    FAULT,                              // Device is in fault state
    OPERATING,                          // Device is in operating in a mode
    IDLE                                // Device is in idle state
};
// Modes of Operation of device
enum ModeOfOperation {
    EDM_ISOFREQUENCY_MODE,              // EDM operating in isofrequency mode, where the frequency of discharges is fixed to the machining frequency
    EDGE_DETECTION_MODE                 // Detect the edge of a conductive workpiece with a single pulse; report the edge via the EDM_FEEDBACK pin
};

// Fault State Types
enum FaultStateType {
    PMM_FAULT_TYPE,                     // Fault state due to the PMM current exceeding the maximum allowed current
    BUCK_CONVERTER_PGOOD_FAULT,         // Fault state due to the buck converter PGOOD pin being low
    BOOST_CONVERTER_PGOOD_FAULT,        // Fault state due to the boost converter PGOOD pin being low
    POWER_OUT_OF_RANGE_FAULT,           // Fault state due to the power input exceeding the maximum allowed power
    HIGH_VOLTAGE_PHASE_SETUP_FAULT      // Fault state due to the high voltage phase setup being incorrect
};

//=============================================================================
// STRUCTURES
//=============================================================================
// Command Parameter Types
struct OutputParameters {
    int dischargeCountTarget;
    float dutyCycle;
    float frequency;
    float initVoltage;
};

// PWM Output Configuration Structure
struct PWMOutput {
    uint32_t slice;
    uint32_t channel;
};

//=============================================================================
// PIN DEFINITIONS
//=============================================================================
// Digital Input/Output Pins
const int EDM_ENABLE              =   2;                // Digital input
const int EDM_FEEDBACK            =   3;                // PWM output for communicating with external motion controller. 
                                                        // (0% duty cycle = at max power setpoint | Decrease motion feedrate, 100% duty cycle = no power consumption | Increase motion feedrate)

const int OUTPUT_OVERCURRENT      =   12;               // Reports when detected current exceeds current limit threshold on output current sensor
const int BUCK_POWER_GOOD         =   13;               // UNUSED
const int BUCK_ENABLE             =   14;               // UNUSED
const int BUCK_ADJ_PWM            =   15;               // UNUSED

const int I2C_SDA_PIN             =   16;               // I2C data pin
const int I2C_SCL_PIN             =   17;               // I2C clock pin

const int BOOST_PGOOD             =   18;               // Reports when boost-converter module is providing power to system, active-LOW when fault is detected
const int PMM_FAULT               =   20;               // Reports problems with power-management module, active-LOW when fault is detected
const int PMM_DIAG_EN             =   21;               // Enables reporting of faults from power-management module
const int PMM_ENABLE              =   22;               // Enables power-management module high-side switch, providing power to system
const int STATUS_LED              =   25;               // Status LED on Pico

// PWM Output Pins
const int SW_HIGH_VOLTAGE_PHASE   =   8;                // PWM #4 Channel A, Switch for connecting high-voltage phase of dual-converter to output. Controlled by P-channel MOSFET (logic is inverted, HIGH = OFF LOW = ON)
const int OUTPUT_OVERCURRENT_SET  =   9;                // PWM #4 Channel B, Sets current limit threshold using PWM, on output current sensor TMCS1133
const int SW_ENABLE               =   10;               // PWM #5 Channel A, Switch for connecting output (-)-electrode to GROUND through output current sensor. Controlled by N-channel MOSFET (Logic is not inverted, HIGH = ON LOW = OFF)
const int SW_HIGH_CURRENT_PHASE   =   11;               // PWM #5 Channel B, Switch for connecting high-current phase of dual-converter to output. Controlled by P-channel MOSFET (logic is inverted, HIGH = OFF LOW = ON)

// Analog Input Pins
const int PMM_ISENSE              =   26;               // Reports current from power-management module current sensor as analog voltage
const int OUTPUT_VSENSE           =   27;               // Reports voltage from output voltage sensor as analog voltage
const int OUTPUT_ISENSE           =   28;               // Reports current from output current sensor as analog voltage

//=============================================================================
// Variables
//=============================================================================

// Machining Parameters for EDM Isofrequency Mode
volatile double machiningDutyCycle = 0.10f;             // Duty cycle for machining (0.0 to 1.0)
volatile int machiningFrequency = 10000;                // Frequency in Hz
volatile int machiningInitVoltage = 80;                 // Initiation voltage in volts

// Telemetry Flag
const bool sendPeriodicTelemetryEnabled = true;             // If true, the device will send periodic telemetry over serial

// Discharge Success Rate Pulse Skipping Feature
const bool allowDischargeSuccessRatePulseSkipping = true;   // If true, the device will pulse skip if the discharge success rate exceeds the maximum discharge success rate threshold
volatile double maxDischargeSuccessRateThreshold = 0.800f;  // Percentage of concurrent-discharges allowed before pulse skipping is triggered. Used to prevent short-circuiting.
                                                            // Can range from 0.000 to 1.000.
volatile int dischargesPerCalculationInterval = 10;         // Number of discharges per calculation interval for discharge success rate calculation

// Power Setpoint Pulse Skipping
const bool allowPowerSetpointPulseSkipping = true;          // If true, the device will pulse skip if the average input power exceeds the maximum input power setpoint
const float MAX_INPUT_POWER_SETPOINT_WATTS = 75.0f;         // The maximum power consumption of the device, to prevent overheating. 
                                                            // The EDM_FEEDBACK pin communicates power consumption to external motion controller via PWM signal
                                                            // (0% duty cycle = at max power setpoint, decrease feedrate | 100% duty cycle = no power consumption, increase feedrate)

// Boost Converter Module Globals 
const int MIN_HIGH_VOLTAGE_PHASE_VOLTS = 64;            // Minimum safe high voltage phase voltage in volts
const int MAX_HIGH_VOLTAGE_PHASE_VOLTS = 100;           // Maximum safe high voltage phase voltage in volts
const int MIN_BOOST_CONVERTER_DPOT_POSITION = 0;        // Minimum position of the digital potentiometer on the boost converter module for safe operation
const int MAX_BOOST_CONVERTER_DPOT_POSITION = 110;      // Maximum position of the digital potentiometer on the boost converter module for safe operation
const int DEFAULT_BOOST_CONVERTER_DPOT_POSITION = 1;    // Default position of the digital potentiometer on the boost converter module
const int BOOST_CONVERTER_RAMP_SPACING_MS = 10;         // Spacing between steps in the digital potentiometer, in milliseconds

//  Parameter Limits
const float MAX_SAFE_INPUT_CURRENT = 7.3f;                      // Maximum safe input current in amps
const float MIN_DUTY_CYCLE = 0.01f;                             // Minimum duty cycle of machining
const float MAX_DUTY_CYCLE = 0.12f;                             // Maximum duty cycle of machining
const float MIN_MACHINING_FREQUENCY_HZ = 5000.0f;               // Minimum machining frequency in Hz
const float MAX_MACHINING_FREQUENCY_HZ = 10000.0f;              // Maximum machining frequency in Hz
const float MIN_ON_TIME_MICROS = 1.000f;                        // Minimum on-time in microseconds
const float MAX_ON_TIME_MICROS = 25.000f;                       // Maximum on-time in microseconds
const float MIN_OFF_TIME_MICROS = 88.000f;                      // Minimum off-time in microseconds
const float MIN_INIT_VOLTAGE = MIN_HIGH_VOLTAGE_PHASE_VOLTS;    // Minimum initiation voltage (exclusive)
const float MAX_INIT_VOLTAGE = MAX_HIGH_VOLTAGE_PHASE_VOLTS;    // Maximum initiation voltage in volts

// Look up table for boost converter module digital potentiometer voltages
volatile int dpotVoltageTable[MAX_BOOST_CONVERTER_DPOT_POSITION + 1];

// I2C Configuration Constants
#define I2C_PORT i2c0                                   // I2C port for the digital potentiometer
#define DPOT_ADDR 0x3E                                  // Address of the digital potentiometer
#define DPOT_REG 0x00                                   // Register address of the digital potentiometer
#define I2C_BAUD_RATE_HZ 10000                          // Baud rate for I2C communication

// System Configuration Constants
const int ADC_RESOLUTION_BITS = 12;                     // ADC resolution in bits (0-4095)
const uint32_t PWM_BASE_CLOCK_FREQ = 133000000;         // Base clock frequency for PWM (133MHz)
const int MAX_PARAMETERS = 4;                           // Maximum number of parameters for command processing
volatile uint32_t edmFeedbackPwmFrequency_Hz = 1000;    // Frequency for EDM_FEEDBACK PWM in Hz (1000 Hz)
const uint16_t EDM_FEEDBACK_PWM_CLOCK_DIVIDER = 10;     // Set to 10 to fit within uint8_t

// Timing Constants
const int PMM_INRUSH_DELAY_MS = 500;                    // Delay after enabling PMM to allow in-rush current to settle
const unsigned long SERIAL_INIT_TIMEOUT_MS = 2000;      // Timeout duration for serial initialization (2 seconds)
const int serialInitializationBlinkInterval_MS = 500;   // Interval for serial initialization (500 ms)
const int periodicTelemetryInterval_MS = 1000;          // Interval for sending periodic telemetry (1000 ms)
volatile int dischargeRateCalculationInterval_MICROS = 0;  // Interval for calculating discharge success rate (is calculated from machining frequency)

// PMM_ISENSE Monitoring Constants
const float ADC_TO_VOLTS = 3.3f / 4095.0f;             // Constant for converting 12-bit ADC into volts
const float PMM_ISENSE_V_PER_AMP = 0.200f;             // 200 mV per amp for PMM current sensor
const int DEVICE_CURRENT_BUFFER_SIZE = 100;            // Size of buffer for device current running average
const int PMM_CALIBRATION_SAMPLES = 100;               // Number of samples to take for PMM current sensor calibration
const int PMM_CALIBRATION_DELAY_MS = 1;                // Delay between PMM calibration samples in milliseconds

// Output Current Sensor Constants
const float ISENSE_OUTPUT_V_PER_AMP = 0.025f;                   // 25 mV per amp for output current sensor (TMCS1133C1A)
const int ISENSE_OUTPUT_AMPS_PER_VOLT = 40;                     // 40 amps per volt for output current sensor (TMCS1133C1A)
const float OUTPUT_CURRENT_ZERO_OFFSET = 0.33f;                 // Zero current offset of output current sensor (TMCS1133C1A), in volts
const int DEFAULT_OUTPUT_CURRENT_THRESHOLD_A = 8;              
const int OUTPUT_CURRENT_SENSOR_CALIBRATION_SAMPLES = 100;      // Number of samples to take for output current sensor calibration
const int OUTPUT_CURRENT_SENSOR_CALIBRATION_DELAY_MS = 1;       // Delay between output current sensor calibration samples in milliseconds

// Output Voltage Sensor Constants
const float OUTPUT_VOLTAGE_SCALE = 0.08090972f;        // Pre-computed (3.3/4095) * 100.4 for output voltage scaling with 99.6:1 voltage divider

// Fault Handling Configuration
const bool PMM_FAULT_IN_USE = true;                     // Should always be true
const bool HIGH_CURRENT_PGOOD_IN_USE = false;           // Set to false if Pi-Filter module is used in high-current phase
const bool HIGH_VOLTAGE_PGOOD_IN_USE = true;            // Set to true if boost-converter module is used in high-voltage phase
const bool dynamicFaultHandlingEnabled = true;          // If true, the device will dynamically handle faults based on the fault type

// Device State Variables
volatile DeviceState deviceState = STARTUP;             // Current device state
volatile DeviceState oldDeviceState = STARTUP;          // Previous device state, used for temporary state storage
volatile ModeOfOperation modeOfOperation = EDM_ISOFREQUENCY_MODE;  // Current mode of operation
volatile FaultStateType FaultStateType = PMM_FAULT_TYPE;// Current fault type
volatile bool modePreparationComplete = false;          // Flag to track if mode preparation is complete
volatile bool isInFaultState = false;                   // Flag indicating if device is in fault state
volatile bool enablePortStatus = false;                 // Status of the enable port

// Timing Variables
volatile unsigned long currentTime_MS = 0;              // Current time in milliseconds
volatile unsigned long lastTelemetryEventTime_MS = 0;   // Time of last telemetry event
volatile unsigned long lastPeripheralManagementEventTime_MS = 0;  // Time of last peripheral management event
volatile unsigned long inrushStartTime_MS = 0;          // Time when inrush started
volatile unsigned long serialInitStartTime_MS = 0;      // Time when serial initialization started
volatile int peripheralManagementInterval_MS = 10;      // Interval for peripheral management in milliseconds
volatile int inrushDelay_MS = 500;                      // Delay for inrush in milliseconds

// Discharge Control Variables
volatile int dischargeCountTarget = 0;                  // Target count of discharges (0 for infinite, positive integer for finite)
volatile int currentDischargeCount = 0;                 // Counter for number of discharges completed
volatile int dischargesSinceOperationStarted = 0;       // Counter for number of discharges since operation started
volatile double dischargeSuccessRate = 0.00f;           // Current discharge success rate
volatile double avgDischargeSuccessRate = 0.00f;        // Running average of discharge success rate
volatile bool requestedDischargesReached = false;       // Flag to indicate if the requested number of discharges has been reached
volatile double newDischargeSuccessRate = 0.00f;        // New discharge success rate

// Current Measurement Variables
volatile double inputCurrentReading = 0.00f;            // Current reading from PMM_ISENSE
volatile int pmmISENSEAdcValue = 0;                     // Raw ADC reading from PMM current sensor
volatile float deviceInputCurrentBuffer[DEVICE_CURRENT_BUFFER_SIZE];  // Circular buffer to store device current samples
volatile int deviceInputCurrentBufferIndex = 0;         // Current index in the circular buffer
volatile bool deviceInputCurrentBufferFull = false;     // Flag to indicate if buffer has been filled at least once
volatile float avgDeviceInputCurrent = 0.0f;            // Running average of device input current (from PMM_ISENSE)
volatile int pmmZeroCurrentOffset = 0;                  // ADC value when no current is flowing
volatile long pmmCalibrationSum = 0;                    // Sum of ADC samples during PMM current sensor calibration
volatile float inputCurrentBufferSum = 0.0f;            // Sum of input current buffer values

// Fault Measurement Variables
volatile double inputCurrentDuringFault = 0.0f;         // Input current reading during fault condition
volatile double outputVoltageDuringFault = 0.0f;        // Output voltage reading during fault condition
volatile double outputCurrentDuringFault = 0.0f;        // Output current reading during fault condition

// Output Current Sensor Calibration Variables
volatile int outputCurrentSensorCalibrationSum = 0;     // Sum of ADC samples during output current sensor calibration
volatile int outputCurrentSensorZeroCurrentOffset = 0;  // ADC value when no current is flowing through output current sensor

// Edge Detection Mode Variables
volatile uint32_t edgeDetectionWrapValue = 0;           // Wrap value for edge detection mode PWM
volatile uint32_t edgeDetectionLevelValue = 0;          // Level value for edge detection mode PWM
volatile bool edgeDetected = false;                     // Flag indicating if an edge has been detected in edge detection mode

// Global PWM Output Configuration
PWMOutput pwmOutputs[4];                                // Array to hold all PWM output configurations

// PWM Setup Values
volatile uint32_t pwmWrapValue = 0;                     // Wrap value for PWM configuration
volatile uint32_t pwmLevelValue = 0;                    // Level value for PWM configuration
volatile uint32_t pwmHighVoltageLevelValue = 0;         // Level value for high voltage phase PWM

// EDM Isofrequency Mode Settings
volatile uint32_t EDMIsofrequencyModeWrapValue = 0;                     // Wrap value for EDM isofrequency mode PWM
volatile uint32_t EDMIsofrequencyModeLevelValue = 0;                    // Level value for EDM isofrequency mode PWM
volatile uint32_t EDMIsofrequencyModeHighVoltageLevelValue = 0;         // Level value for high voltage phase PWM in EDM isofrequency mode
const uint32_t EDMIsofrequencyModeHighVoltagePulseOnTimeMicros = 1;     // Fixed 1μs on-time for high-voltage pulse. Used to calculate level for high voltage phase PWM output. Prvents shoot-through failure. 
const double EDMIsofrequencyModeHighVoltagePwmOffsetValue = 0.25f;      // Offset value for high voltage phase PWM output. Used to calculate level for high voltage phase PWM output. Prevents shoot-through failure.
volatile unsigned long lastDischargeSuccessRateCalculationTime = 0;     // Time when discharge success rate was last calculated

// Discharge Measurement Variables
volatile bool newDischargeDetected = false;              // Flag to indicate when a new discharge is detected
volatile double newDischargeCurrent = 0.0f;              // Current value of the most recent discharge
volatile int newDischargeCurrent_ADC = 0;                // ADC reading for the current of the most recent discharge
volatile double newDischargeVoltage = 0.0f;              // Voltage value of the most recent discharge
volatile int newDischargeVoltage_ADC = 0;                // ADC reading for the voltage of the most recent discharge
volatile double avgDischargeCurrent = 0.0f;              // Running average of discharge current
volatile double avgDischargeVoltage = 0.0f;              // Running average of discharge voltage

// Output Current Sensor Threshold Variables
volatile float outputOvercurrentThresholdVoltage = 0.0f;                // Voltage threshold for output current sensor
volatile int outputOvercurrentThresholdLevel = 0;                       // PWM value for output current sensor threshold
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
void loop() {
     // Record the current time in milliseconds
    currentTime_MS = millis();
    // If the device is in the FAULT state, run the fault handler function. It will act in accordance with the fault state type
    if (deviceState == FAULT) {
        handleFault();
    }
    // Switch statement for device states of secondary priority
    switch (deviceState) {
        case PERIPHERAL_MANAGEMENT:
            // Case for PERIPHERAL_MANAGEMENT state
            handlePeripheralManagement();
            break;
        case OPERATING:
            // Case for OPERATING state
            handleOperatingState();
            break;
        case IDLE:
            // Case for IDLE state
            handleIdleState();
            break;
    }
    // If periodic telemetry is enabled, and the time since the last telemetry event is greater than the telemetry interval, send telemetry
    if (sendPeriodicTelemetryEnabled && currentTime_MS - lastTelemetryEventTime_MS >= periodicTelemetryInterval_MS) {
        sendTelemetry();
        lastTelemetryEventTime_MS = currentTime_MS;
    }
    // If the time since the last peripheral management event is greater than the peripheral management interval, set the device state to PERIPHERAL_MANAGEMENT
    if (currentTime_MS - lastPeripheralManagementEventTime_MS >= peripheralManagementInterval_MS) {
        // Store the current state of the device, so that after the peripheral management loop, the device state can be restored to the previous state to continue what it was doing before
        oldDeviceState = deviceState;
        // Set the device state to PERIPHERAL_MANAGEMENT, so that we can enter the peripheral management loop
        deviceState = PERIPHERAL_MANAGEMENT;
        // Update the last peripheral management event time
        lastPeripheralManagementEventTime_MS = currentTime_MS;
    }
}

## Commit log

2025-06-02 initial commit from Powercore Development Repo
    [0679H9120-05.step, 0906-8-15-20-76-14-11-0.step, 226TTA350M.step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]
2025-06-24 removed buck converter files
    [buck-converter.kicad_sch, dual-converter-buck-module-V1.0.kicad_pcb, dual-converter-buck-module-V1.0.kicad_sch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]
2025-06-24 schematic PDFs
2025-06-24 Formatting, License, and Powercore Name
    Minor formatting fixes, updated license to be more representative of actual license. Made "Powercore V3" name consistent throughout document. Made trademark language clearer. Removed copyright symbol.
2025-06-25 Update powercore-v3-waveform-06.png
    spelling error in scope cap fixed
2025-07-04 sim diodes
2025-07-05 footprint #D file location
    [dual-converter-boost-converter-module-V1.0.kicad_pcb, dual-converter-pi-filter-module-V1.0.kicad_pcb]
2025-09-08 firmware 1.1.0-beta
    - 10 KHz
    - 10% Duty Cycle
    - 64- 100 V
    - 75 W power setpoint
2025-09-08 updated specifications for RevG
    - max dutycycel reduced from 15% to 10%
    - max voltage decreased from 150V to 100V
    - max frequency decreased from 20,000 to 10,000 Hz
    - PWM feedback reports power consumption
